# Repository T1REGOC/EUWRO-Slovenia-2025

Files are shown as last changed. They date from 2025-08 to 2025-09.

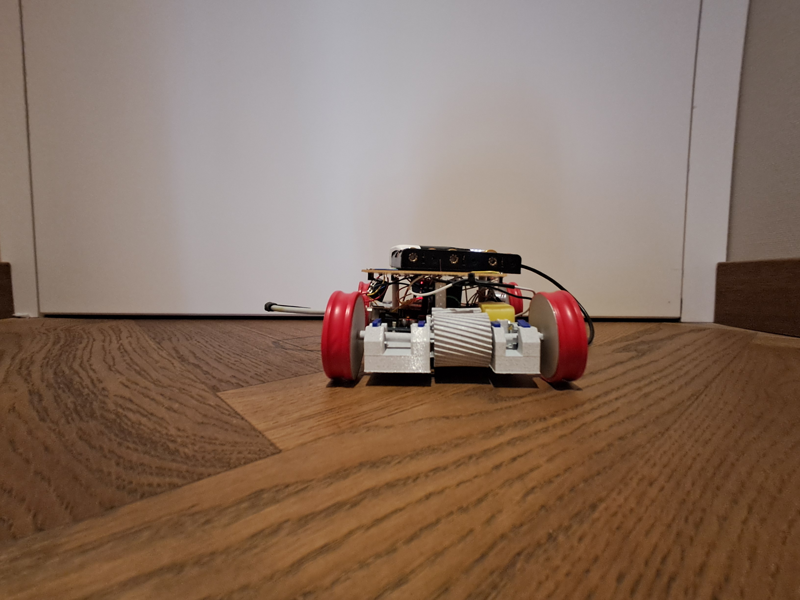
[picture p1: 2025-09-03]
Vehicle photos/Rear.jpg

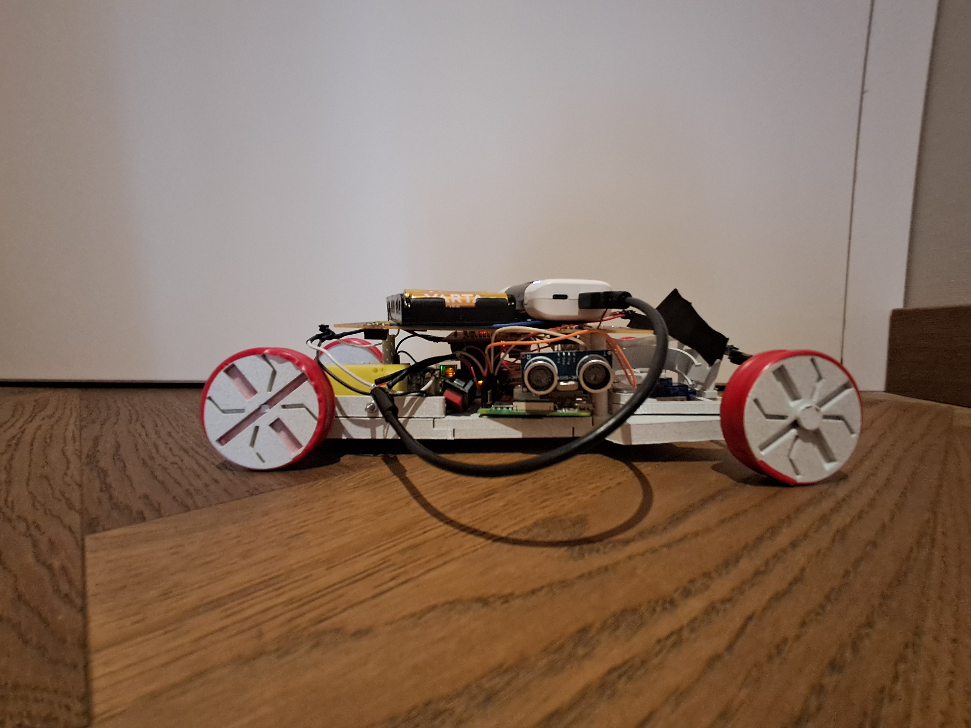
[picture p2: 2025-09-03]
Vehicle photos/Right.jpg

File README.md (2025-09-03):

This is a completely new, special repository made just for the competition in Slovenia, but here is an older version:

https://github.com/T1REGOC/WRO-2025-Season

# REGOČ | EUWRO-Slovenia

<center> <center>

## TABLE OF CONTENT

| Section  | Explanation |
| --  | -- |
| [PROBLEM](#problem)  | Adressing the task of the competition. |
| [ENGINEERING MATERIALS](#engineering-materials)  | The list of everything we used. |
| [MOBILITY MANAGMENT](#mobility-managment)  | [Driving](#driving),  [steering](#steering)| 
| [POWER AND SENSE MANAGMENT](#power-and-sense-managment)  |  [Power supply](#power-supply), [sensorics](#sensorics)  |
| [PICUTRES](#pictures)  |  [Team pictures](#team-pictures), [vehicle pictures](#vehicle-pictures)  |
| [ASSEMBLY INSTRUCIONS ](#assembly-instructions)  |  [Hardware](#hardware), [software](#software)  | 
| ---| --- |
| [3D FILES](https://github.com/T1REGOC/EUWRO-Slovenia-2025/tree/main/3d%20Models)| Files of our robot. |
| [SRC](https://github.com/T1REGOC/EUWRO-Slovenia-2025/tree/main/src) |Code. |
| [SCHEMES](https://github.com/T1REGOC/EUWRO-Slovenia-2025/tree/main/schemes)| Schemes of...  |
| [VIDEOS](https://github.com/T1REGOC/EUWRO-Slovenia-2025/tree/main/videos)| Videos of our robot. |

# PROBLEM
The goal of the Future Engineers WRO category is to design a fully autonomous vehicle that completes two different challenges in 3 minutes. The direction of the vehicles movement, position of the interior walls  and their size in both challenges is randomized before the start of the round, so the vehicle should recognize whether to turn left or right by itself. 
This is our playfield:
<br><br>
    


<br><br>
### OPEN CHALLENGE
In the open challenge, once the robot starts, its goal is to complete 3 laps around the map while avoiding the walls and finish in the same zone it started in.
For the Open Challenge we use ultrasonic sensors to make sure the vehicle is centered at all times, that is why we have ultrasonic sensors on both sides, and while the vehicle is centering it also looks for a pattern using the camera.
We needed to take a look at the map again:



By thinking a little bit you can see that if your direction is clockwise you will pass the lines always going orange first and then blue, but if you are going counter-clockwise you will always go blue first and then orange. We did not recognize this at first, but after a few months of working on the robot it was almost like a key, because our most unpredictable sensor from the last robot(the color sensor APDS-9960) did not give accurate results so we would want to remove it in this one. That is when we got the idea that the passing of the lines(orange-blue or blue-orange) is a pattern and we could use tensorflow for that because what is a machine learning model best at? You're right, looking for patterns. Using tensorflow we would make a model that had these possible outputs(orange-blue, blue-orange or none), it is pretty straight-forward to how we would adapt looking at the output, if the camera saw orange-blue it steers right, blue-orange it steers left, then we count the times that we passed the lines and when it hit 12(3 laps) we stop.

### OBSTACLE CHALLENGE 
In the obstacle challenge, once the robot starts, its goal is again to complete 3 laps but now other than avoiding walls it has to avoid red and green pillars which are in the way. Depending on the color 
it passes the pillars either from the left or the right (robot passes pillar on the right if he sees red, and on the left if he sees green). Once the 3 laps are complete and robot is back in its starting area it should parallely park in the previously set
parking spot. The parking spot is 1.5x the lenght of the vehicle. The vehicle may also start from the parking spot. 
So how did we do it? We first thought about using just RGB and opencv, but we researched about the color formats and we did not want to use RGB after that because we found the superior one: HSV(Hue, Saturation, Value). So you might ask why we use this instead of RGB, its simple:
1. It seperates color(hue) from brightness(value) and saturation colour intensity.
2. It is more robust to lighting changes than RGB.
3. It makes it easier to define color ranges for masking
4. RGB mixes color and brightness, so the same color can look very different under different lighting.
HSV allowed us to filter by hue, making color detection more reliable. But we dont want to solely depend on just opencv, we want to make it both more reliable and more educational therefore we added tensorflow. This time we made a model with tensorflow that looked for green or red pillars, so then in the code we made it so even though opencv saw the pillar it has no power because tensorflow was our priority. So the only way that a pillar would be detected and accepted is for our tensorflow model to find it.
Now we fixed the problem with the pillars, we gotta get the parking right, for parking we use ultrasonic sensors and also decided to use 2 instead of 1 ultrasonic sensors on the sides(you will see why in a bit), so depending on what is our steering side the parking will always be opposite(if you steer right the parking is on the left) and we would use that to our advantage, so for the parking after the last steering we would "line up" the vehicle for parking by looking at the differences of distance that the ultrasonic sensors give on the same side, so for example if the vehicle is at a 30 degree angle from the wall back sensor would give 3cm and the front one would be 8cm, what we would do in this scenario is steer the vehicle depending on which number is bigger and which side it was, and we would do this until the difference would be under 2cm.
#### PARKING
Now that we are lined up to the wall we dont want to steer until we actually need to park in, so now we look for the parking also using ultrasonic sensors but now looking solely on the back side sensor, why? Because the parking walls are 20cm wide and passing by our sensor would see this(25,25,27,28,28,2,2,28) so if you dont understand those would be the example readings from the sensor and we knew when we hit the parking spot when we would hit a "drastic change" often going in a number that is under 10cm, but we cant steer yet because we hit the first part of the parking and we want to parralel park so we need to hit the second part of the parking, we just go straight and look for another drastic change again, when we see it that means that the back side sensor(almost where the back wheels are) is at the second part of the parking, so now we reverse and steer until our back sensor hits under 5cm and then go forward and steer to line up.
   
# ENGINEERING MATERIALS
- Servo SG90 (23 x 12 x 29 mm) ( Why we chose it: reliable, small, previusly available to us )
  datasheet: http://www.ee.ic.ac.uk/pcheung/teaching/DE1_EE/stores/sg90_datasheet.pdf


- Yellow TT Gear Motor (71 × 22 × 37 mm) ( Why we chose it: enough torque (further explained later on) , previously available to us, reliable )
  datasheet: https://media.digikey.com/pdf/Data%20Sheets/Adafruit%20PDFs/3777_Web.pdf 


- HC - SRO4 Ultrasonic sensor (x6) (43 x 20 x 15 mm)
  datasheet: https://cdn.sparkfun.com/datasheets/Sensors/Proximity/HCSR04.pdf


- Raspberry Pi Camera v2 (25mm x 23mm x 9mm)
  datasheet: https://www.farnell.com/datasheets/2056179.pdf?_ga=1.152577328.880870297.1479740269


- DHT11 (15.5 x 12 x 5.5 mm)
  datasheet: https://www.mouser.com/datasheet/2/758/DHT11-Technical-Data-Sheet-Translated-Version-1143054.pdf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


- Arduino Uno (69 x 54 mm)
  datasheet: https://docs.arduino.cc/resources/datasheets/A000066-datasheet.pdf


- Raspbbery Pi 4 (86 x 57 mm)
  datasheet: https://datasheets.raspberrypi.com/rpi4/raspberry-pi-4-datasheet.pdf


-PLA (3D printing materials)

# MOBILITY MANAGMENT
Considering we 3D designed everything ourselves, we decided to split the vehicle in three parts: the front ( steering ), the rear  ( drive ) and the middle ( connection beetween two ).They are connected so that the top part of the drive and the bottom part of the middle part allign and then we screw through both of them.  We did that so that if there is failure for example the steering, we do not have to print it all again, but just the steering part. That is also why we tried to design everything so that we can tighten it by screws. 

The round pillars that rise from the pplatforms are holders for the protoboard. 

Because of our modularity, considering the robot isn't printed as whole it bends more, so we decided to print little bend preventers. They are designed so that thay fight very tightly over the connction of the segments. They are U shaped, 20 mm wide. 

## DRIVING
For the driving power, the motor, we decided to go with TT Yellow Gear Motor because it was strong enough, reliable, affordabble and available to us. 

Motor torgue – 0,8kg / cm 
Gear output torque – 1.6kg/cm  ( gear ratio == 1:2 ) 
Torque on wheels – 1.4 kg/cm ( gear output torque  - min. 10%)

Formula for torque when the gear ratio is 1:2

T = (Mt * 2) – (Mt*2 *10%)

T = Final torque on wheels
Mt – Motor torque

We stabillised it to the platform by designing a holder for it. It is placed longitunally. 
With two helix gears, whose ratio is 1:2 (so that we gain torque since the speed is not as necessary), we created a transmission.
Why helix gears?
We thought about using double helix gears because they have a great grip, but considering that we wanted most of the parts to be modular, the double helix gears would be harder to dismantle and mantle each time. 
The first, main gear has 16 teeth and is 15.6mm in diameter, 32.5mm in lenght. From one side it is span by the motor, and from the other, just to stop its lean it is supported by a little holder. 
To the second, drive gear (30mm diameter, 32.5mm, 32 teeth ), we created a plus shaped hole since we needed the shaft to rotate with the gear. The two shafts are also plus shaped and connected by a plus shaped connector. They have plates so that they don't move left / right thorugh the gear. At the end there is a rectangular hold for the wheels. 

Here it is all together:

 

## STEERING
For the steering, we went with a always reliable, stable, small, affordable and available SG90 servo motor. We decided on the Ackermann's steering system since it
seemed more stable than pivot point turning or others. 
This is an example of the Ackermann's steering system.



You design a servo addon that rotates the middle connector. The two side motor hubs are pivotted at one point and on the other connected to the middle shaft. On the hubs go wheels. When the servo rotates, the addon rotates with it and moves the connector left aand right. Then the motor hubs rotate because of the pivot on the other side.  

Considering that upfront we don't have driving power, the wheels must be able to rotate freely. So the shaft that they go on is a bit lose, so the wheels have the abilty to rotate and then just tighten it up with a designed screw. The wheels will spin when the 
drive wheels start to spin.

Because thec camera is infront of the steering, but has to cross over the steering to get to the raspberry, we designed a little bridge so that the camera cable doesn't block our steering. 

Max. Steering angle == 30°



<br><br><br>
Here it is all together:



# POWER AND SENSE MANAGMENT

Electrical scheme



## POWER SUPPLY
As for the competition at the national championship in Samobor, we will use a portable charger to power our autonomous robot. The charger we use is small so it will not take up too much space on the robot. This charger also has an on/off button, which can be used to turn the robot on and off. This charger outputs 5V and 3A, which is ideal for powering our autonomous robot. Portable chargers also use a BMS (battery management system) which ensures that the battery is safe and reliable. With the BMS, we can see things like battery charge, battery capacity, and we can get feedback about any problems with the battery. Our charger has a light indicator for battery charge. BMS is also used to balance cells (if some are discharged or overcharged), prevents overvoltage, underdischarge, overcurrent, and overheating.

---
## SENSORICS

- Selection


The selection of sensors for our project was carried out systematically. For each potential component, we carefully considered not only its advantages but also every possible limitation or drawback it could introduce. This iterative process—selecting, evaluating, and refining—ensured that the final sensor set was both practical and effective for our goals.

- Ultrasonic sensors
  
One of the key design decisions was to integrate two ultrasonic sensors, positioned on both sides of the robot instead of relying on a single unit. This configuration allows the robot to align itself precisely with walls, which can then be leveraged for autonomous steering without depending solely on the camera system. By doing so, we enhanced both the reliability and independence of the navigation process.

- Digital Temperature and Humidity sensor
  
Additionally, we incorporated a DHT11 sensor to measure ambient temperature and humidity. These values directly influence the speed of sound in air, and by accounting for them, we can improve the accuracy of distance measurements from the ultrasonic sensors. This consideration highlights the importance we placed on precision and robustness in the sensor design. Therefore instead of the fixed speed of sound at 343m/s we made it a variable, and this is the formula we used:

`Speed_of_sound(m/s) = 331.4 + 0.6 * temperature(°C) + 0.0124 * Humidity(%)`

---
# PICTURES
## TEAM PICTURES
teamofficial

Left: Gabriel , Middle: David, Right: Vedran

funnypic

Funny picture

## VEHICLE PICTURES
Rear



Left



Right



Top


Front


<br><br><br>
# ASSEMBLY INSTRUCTIONS
## HARDWARE

List of materials:
All of the 3d prints, and engineering materials + M2 & M3 set of bolts amd nuts

### 1. PLATFORM
Place the front / rear platform next to the middle one so that the holes for the screwes corespond and then screw it. 
<br>

### 2. DRIVE
1. Install the motor inside his holder.
    - Put the motor in the holder and screw it.
    - Don't screw the holder to the platform!
2. Insert the small gear in the holder and the motor shaft on the other end.
3. Install the motor to the platform.
4. Big gear preparation
    - Take the two shafts and insert them in the gear until they are connected.
    - Put the cards on the shaft ( 2 on each side) corespondingly to the card holder holders.
5. Lower the big gear with card holders in their place.
6. Screw the cards to their holders.
7. Place the wheels at the end of the shaft.
<br><br>

### 3. STEERING
1. Place the servo in its place and screw it.
2. Place the left and the right arms in their position
3. Place the connector so that it captures both the left and the right arm.
4. Cover them up with coresponding covers.
5. Place the servo addon so that it connects from the middle of the connector to the servo.

## SOFTWARE
#### 1. Arduino Uno
1. Arduino IDE
    - Download and install the official Arduino IDE from [https://www.arduino.cc/en/software]
    - This software allows you to write code(called sketches), compile them, and upload them to your Arduino board

    **Setup**
    - Connect the Arduino Uno to your computer using a USB cable
    - Open the Arduino IDE and select your board:
        - Go to Tools - Board - Arduino AVR Boards - Arduino Uno

    **Uploading the program**
    - Open the sketch you want to run, for this robot specifically you want the one that says "THIS RUNS ON THE ARDUINO UNO"
    - Click the Upload button and the IDE will compile the code and upload it to the Arduino
    
    **Auto-running the program**
    - Once the code is uploaded the sketch is stored in the Arduino memory
    - Whenever the board is powered, the program will automatically start running, therefore you dont need any additional setup
    The Arduino Uno is successfully setup!

#### 2. Raspberry Pi 4
1. Raspberry Pi OS
    - Download and install the official Raspberry Pi Imager from[https://www.raspberrypi.com/software/]
    - This software will allow you to download and write various operating systems to a microSD card
    - In this case you want to choose Raspbian on the Operating System tab, and then choose your desired SD Card. When the OS is written on the SD Card you will want to insert it into the SD Card compartment on the Raspberry Pi 4

    **Setup**
    - You can either connect the Raspberry Pi to a monitor using its micro HDMI output or do everything with VNC(without contact). Since using a monitor and a micro HDMI cable is more intuitive you can use that option.
    - Now you will want to transfer the codes that say "THIS RUNS ON THE RASPBERRY PI" onto the Raspberry Pi 4.

    **Auto-running the program on start**
    - Open command prompt and run `sudo nano /etc/rc.local`
    
    Explanation:
    - sudo - run with administrator rights(needed because /etc/rc.local is a system file)
    - nano - text editor used to open the file
    - /etc/rc.local - a script that runs automatically at the end of every boot process on Linux

    - Now you will want to add the line
     `sudo bash -c 'sudo python3 /home/pi/<<directory>>/<<filename.py>>' &` before the line `exit 0` and save and close

    Explanation:
    - sudo - run as root(administrator)
    - bash -c ' ... ' - tells bash to run the command inside the quotes
    sudo python3 /home/pi/.../filename.py - runs the Python program as root using python3
    - & - runs the command in the background, so the system can continue booting without waiting for Python script to finish

    Reboot the Raspberry Pi and it will be ready to use!

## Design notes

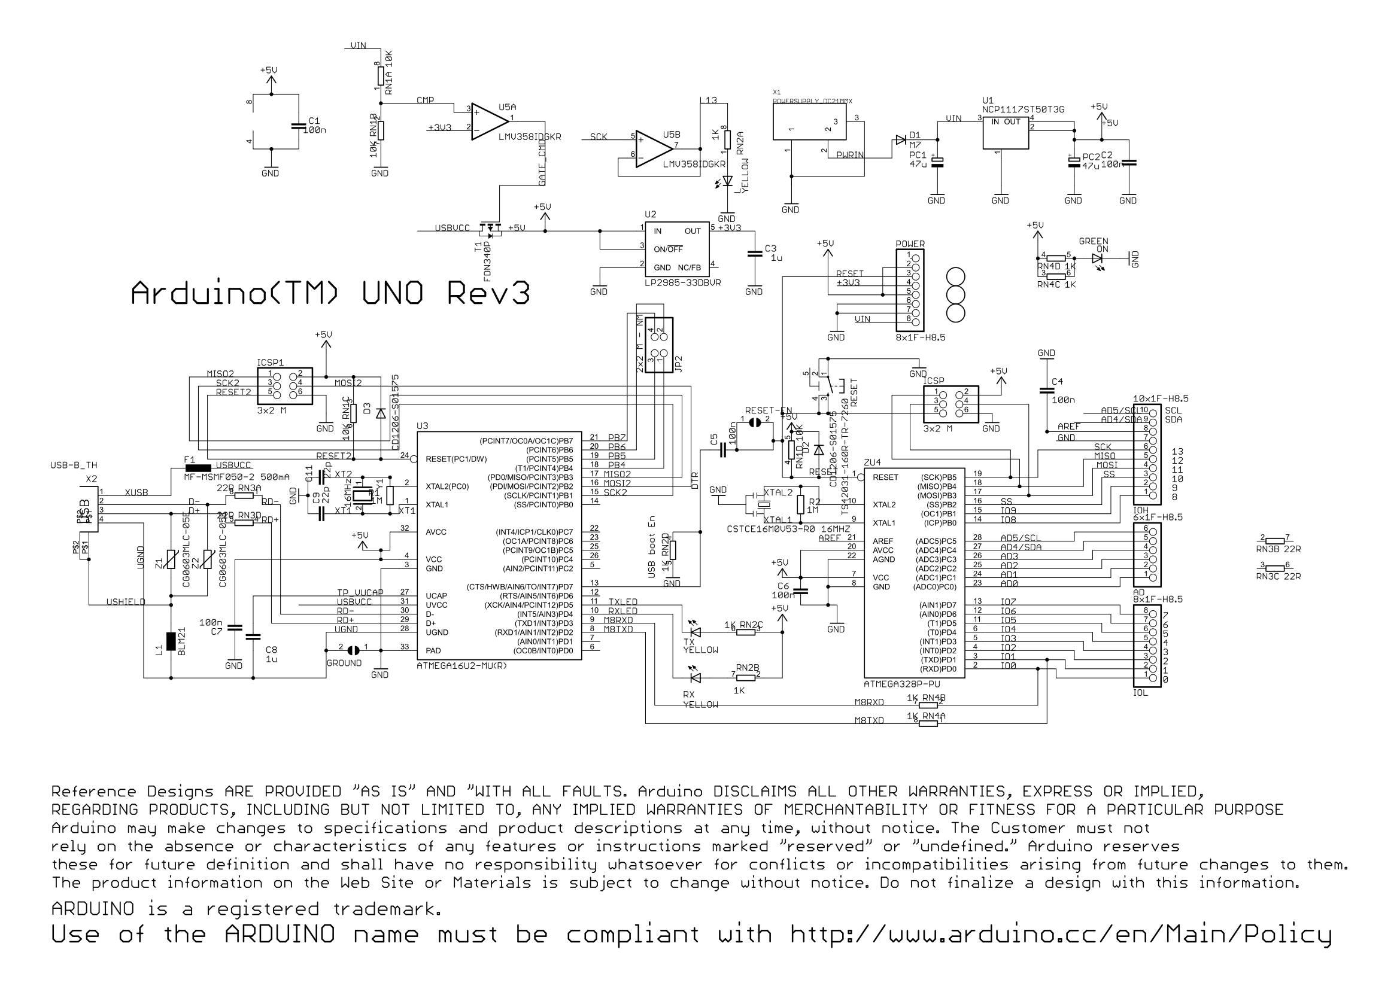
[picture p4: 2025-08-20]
schemes/Arduino_Uno_Rev3-schematic-1.png

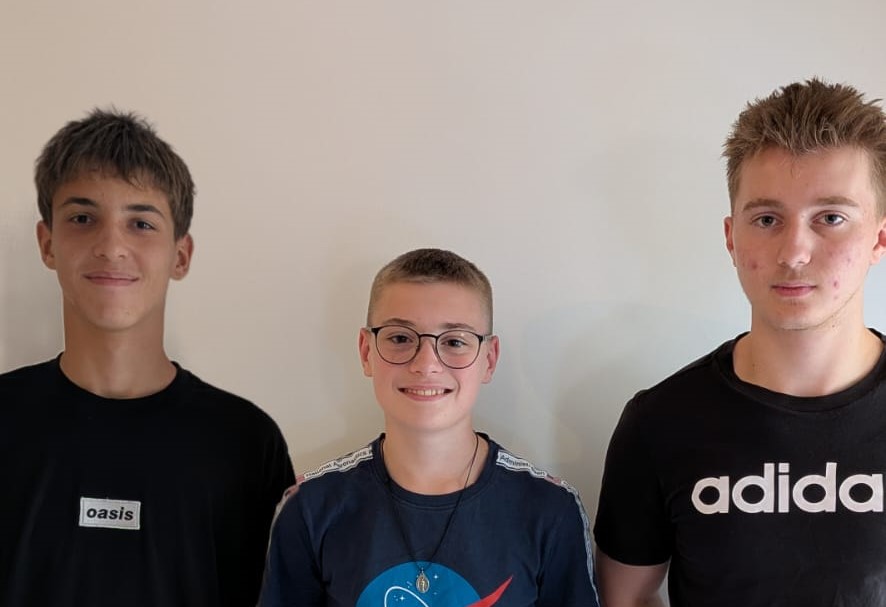
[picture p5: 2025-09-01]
Team photos/teamofficial.jpeg

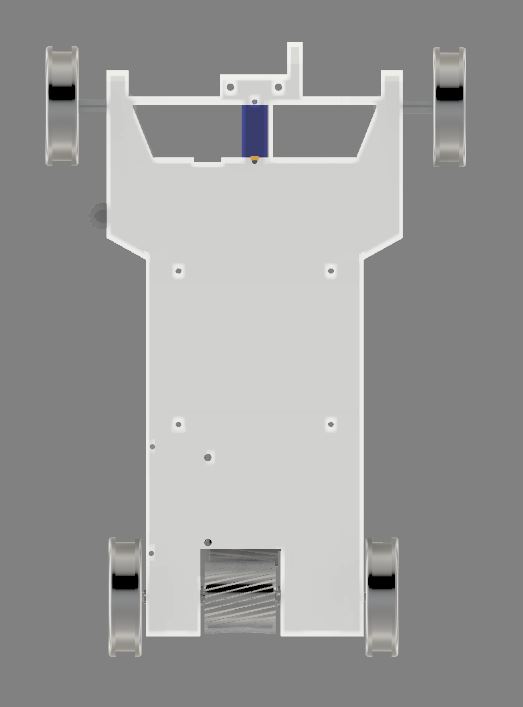
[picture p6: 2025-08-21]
Vehicle photos/bottom.JPG

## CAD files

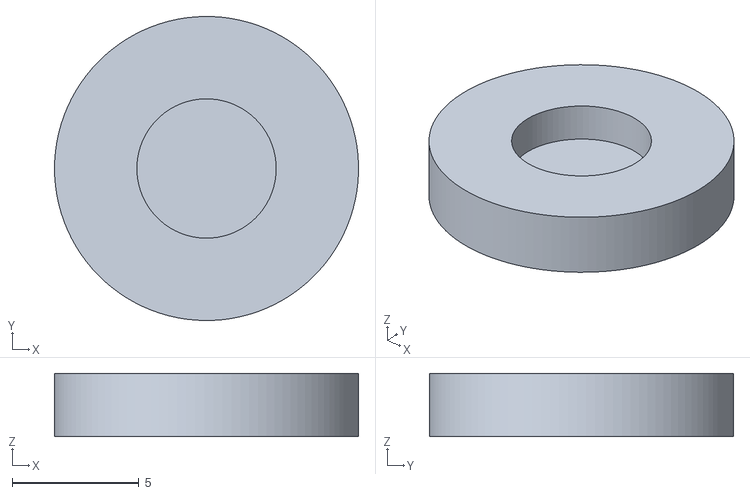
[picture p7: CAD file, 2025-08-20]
3d Models/poklopacox2.stl
12.0 x 12.0 x 2.50

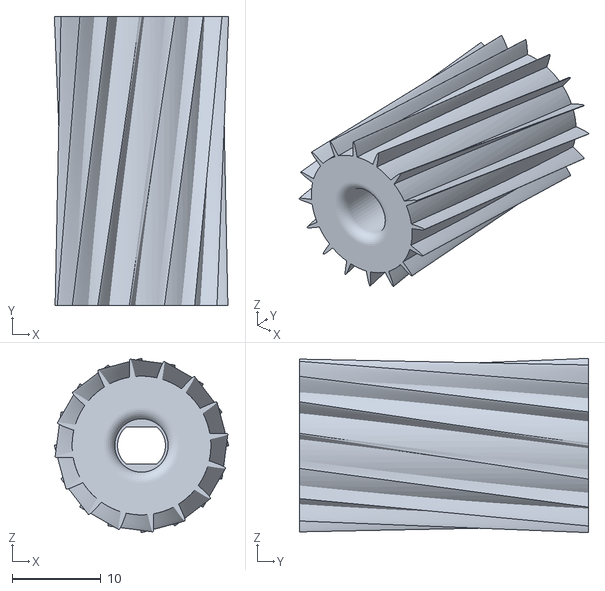
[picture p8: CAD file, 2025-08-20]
3d Models/maligear.stl
19.6 x 32.5 x 19.6

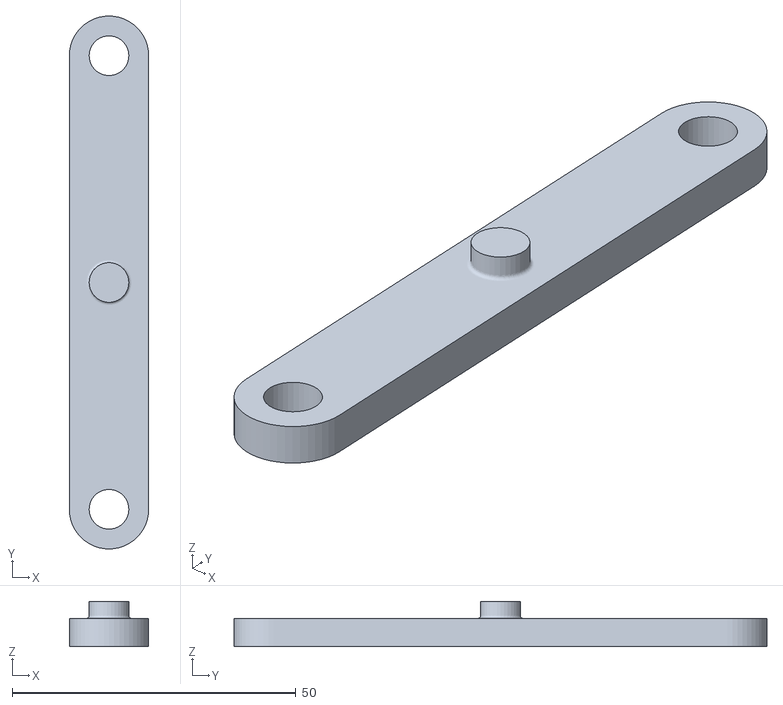
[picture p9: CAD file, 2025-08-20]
3d Models/connector.stl
14.0 x 94.0 x 8.00

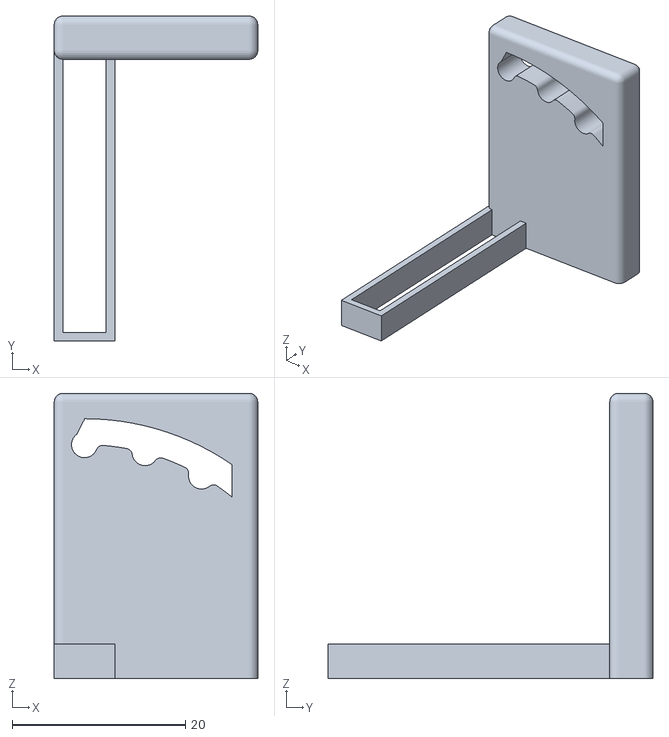
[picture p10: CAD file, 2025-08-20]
3d Models/kamerapoomično.stl
23.5 x 37.5 x 32.9

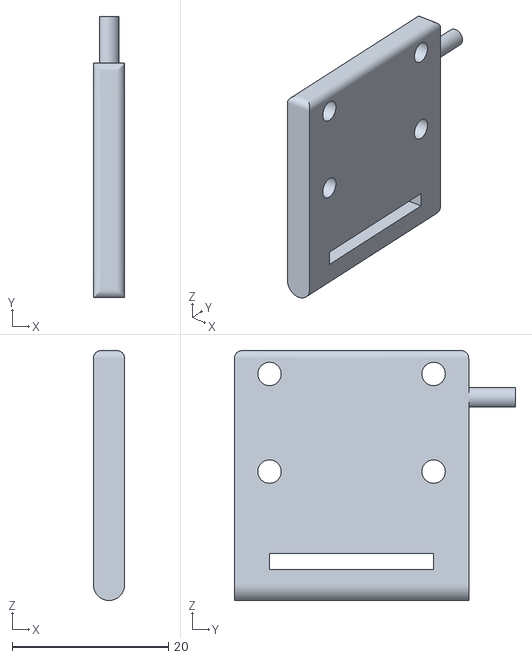
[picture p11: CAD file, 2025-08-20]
3d Models/kameraholder.stl
4.00 x 36.0 x 32.0

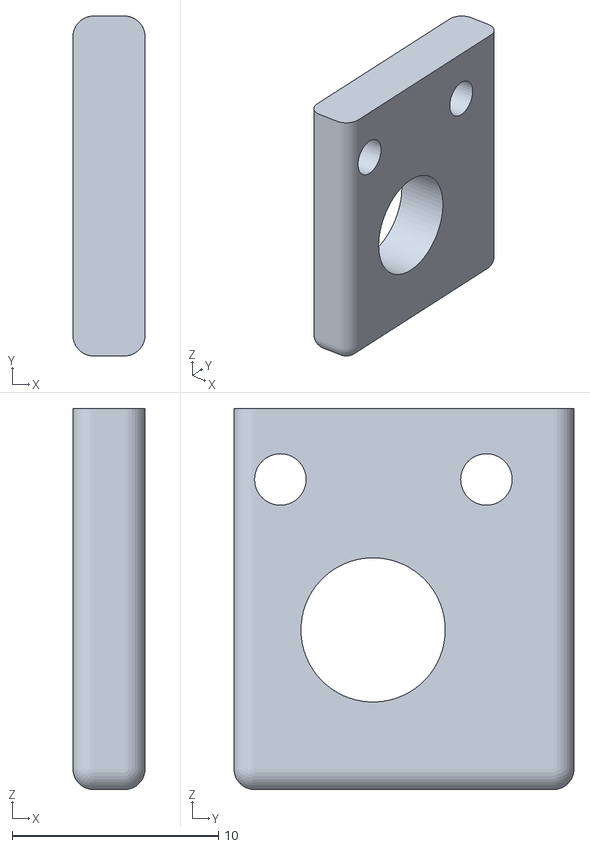
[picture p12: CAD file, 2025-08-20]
3d Models/kartica.stl
3.50 x 16.5 x 18.5

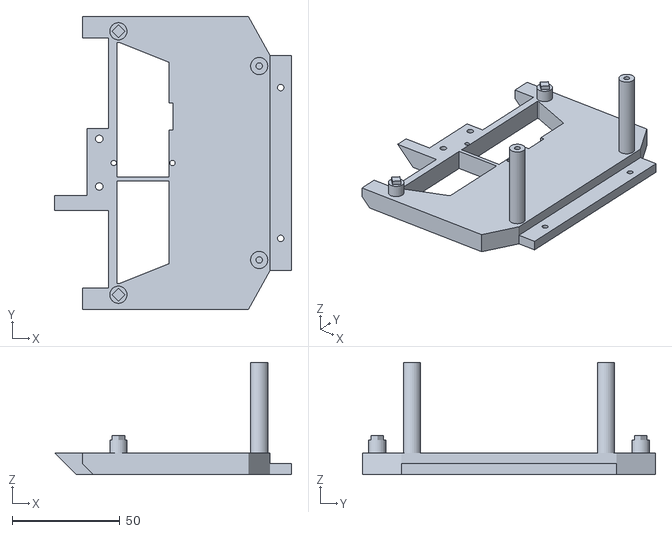
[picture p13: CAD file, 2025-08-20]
3d Models/tijeloskretanje.stl
110.0 x 136.0 x 52.0

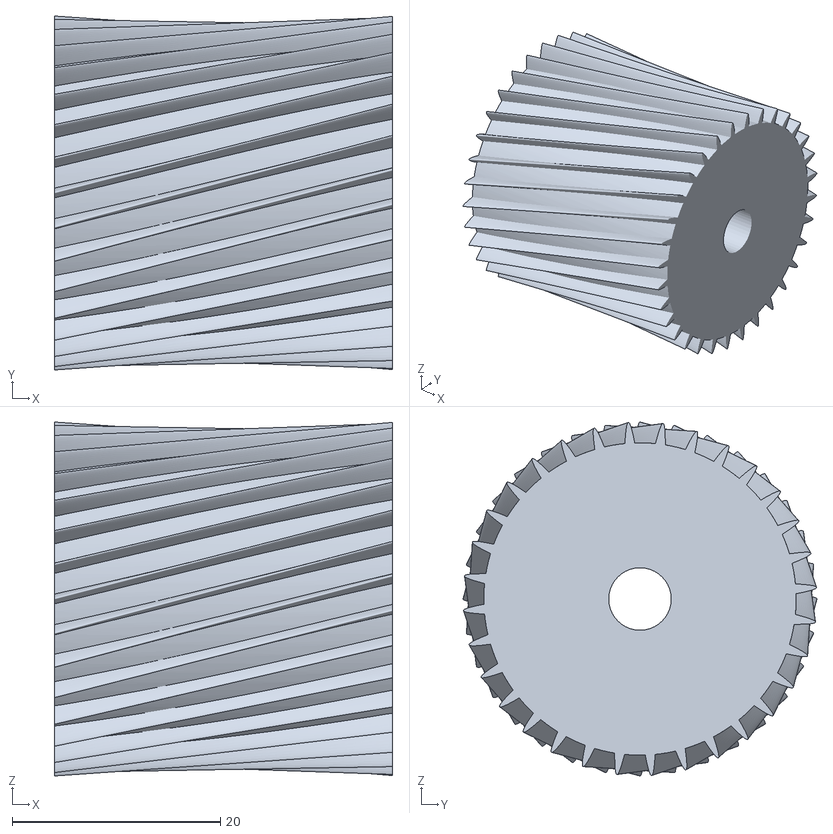
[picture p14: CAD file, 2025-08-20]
3d Models/velikigear.stl
32.5 x 34.0 x 34.0

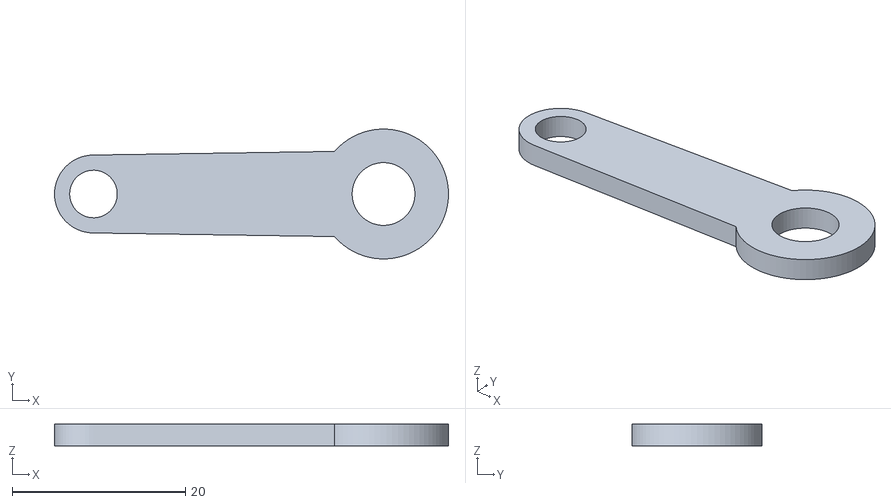
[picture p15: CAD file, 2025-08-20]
3d Models/servoaddon.stl
45.5 x 15.0 x 2.50

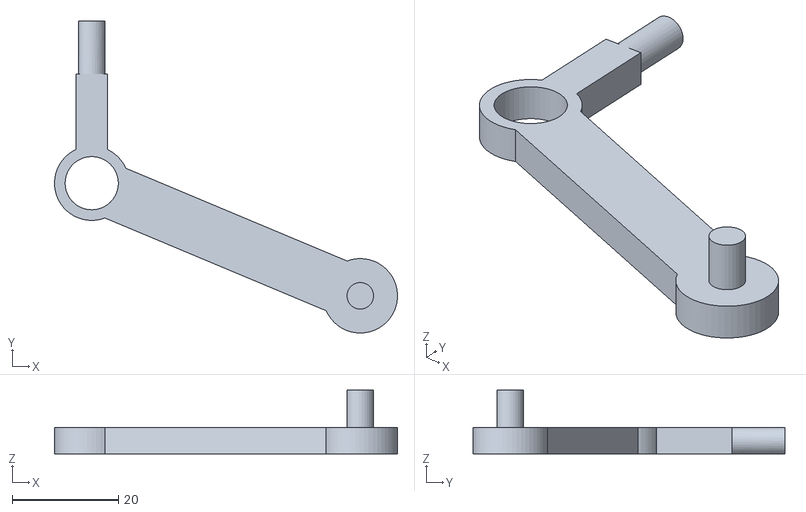
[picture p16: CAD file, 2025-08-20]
3d Models/desninosač.stl
64.5 x 58.7 x 12.0

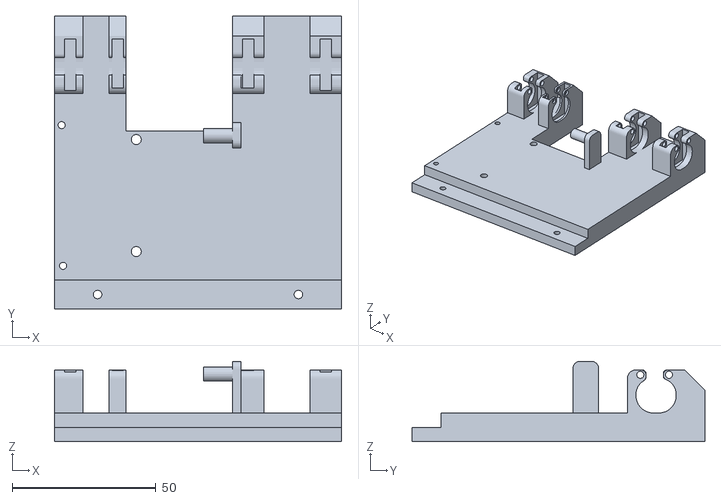
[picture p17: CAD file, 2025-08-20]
3d Models/tijelopogon.stl
100.0 x 102.0 x 28.0

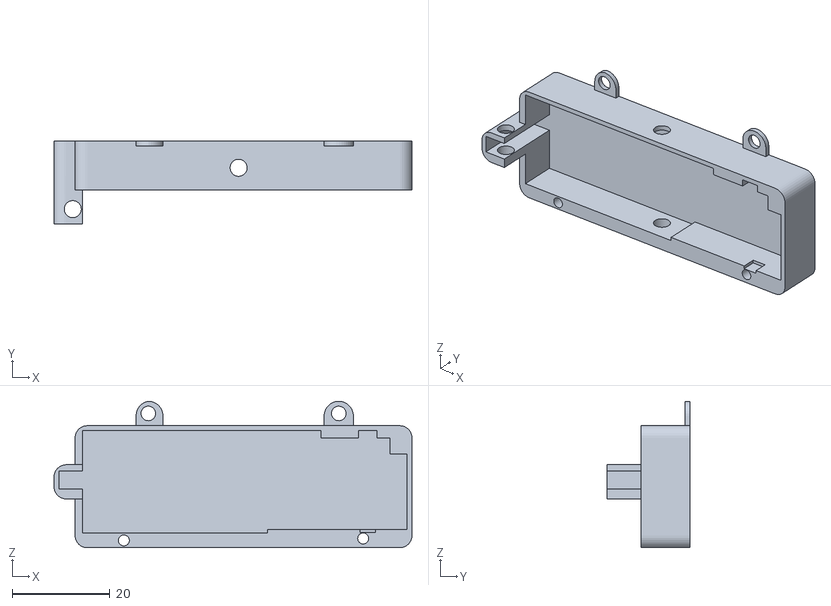
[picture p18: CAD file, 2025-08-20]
3d Models/motorholder.stl
73.3 x 17.0 x 30.0

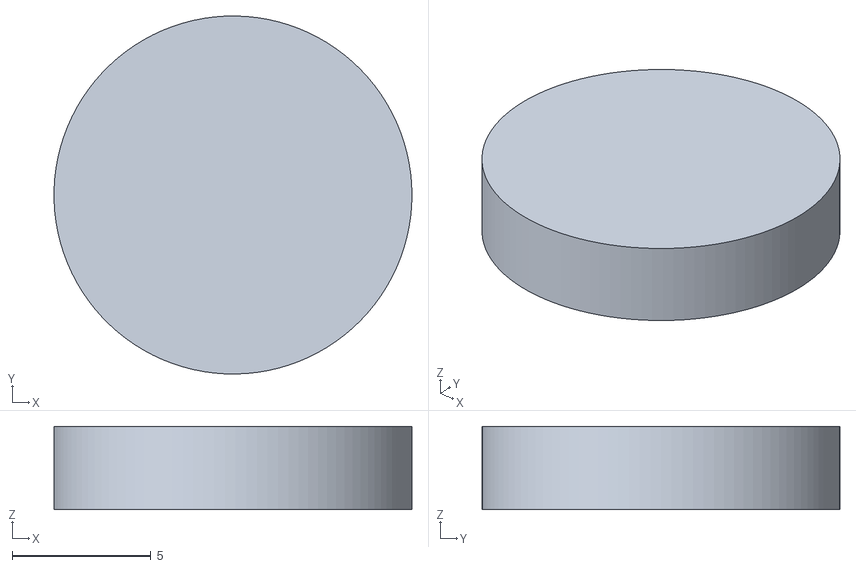
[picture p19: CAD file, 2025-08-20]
3d Models/poklopackx2.stl
12.9 x 12.9 x 3.00

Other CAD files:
3d Models/lijevinosač.stl

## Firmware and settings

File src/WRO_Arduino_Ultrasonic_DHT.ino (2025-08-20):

// THIS CODE IS FOR THE ARDUINO UNO //
//            TEAM REGOC            //
#include <DHT11.h>  // Include the DHT sensor library to read temperature and humidity data.
#include <NewPing.h>  // Include the NewPing library to control ultrasonic sensors.
#include <Wire.h>
#include <Servo.h>

#define APDS9960_ADDR 0x39 // I2C address for the APDS9960 sensor.
#define ENABLE_REG 0x80 // Register address for enabling the APDS9960 sensor.
#define ATIME_REG 0x81 // Register address for the APDS9960 sensor's integration time.
#define CONTROL_REG 0x8F // Register address for controlling the APDS9960 sensors gain and other settings.
#define CDATAL_REG 0x94 // Register address for reading color data from the APDS9960 sensor.
#define trigPin 2  // The trigger pin for all the ultrasonic sensors (sending the pulse).
#define echoPin1 3  // The echo pin for the first ultrasonic sensor.
#define echoPin2 5  // The echo pin for the second ultrasonic sensor.
#define echoPin3 6  // The echo pin for the third ultrasonic sensor.
#define echoPin4 7  // The echo pin for the fourth ultrasonic sensor.
#define echoPin5 8  // The echo pin for the fifth ultrasonic sensor.
#define echoPin6 9  // The echo pin for the sixth ultrasonic sensor.
#define dhtPin 4  // The data pin for the DHT22 sensor.
#define maximum 400  // Maximum range of the ultrasonic sensors in cm.

DHT11 dht11(4); // Initialize the DHT11 sensor object on pin 4.

Servo stmotor;
//steering motors for detection
#define m1 12
#define m2 A0
#define m3 A1
#define m4 A2

//speed motors
#define s1 10
#define s2 11

// power pins for speed
#define p A3

NewPing sonar1(trigPin, echoPin1, maximum);  // Initialize the first ultrasonic sensor.
NewPing sonar2(trigPin, echoPin2, maximum);  // Initialize the second ultrasonic sensor.
NewPing sonar3(trigPin, echoPin3, maximum);  // Initialize the third ultrasonic sensor.
NewPing sonar4(trigPin, echoPin4, maximum);  // Initialize the fourth ultrasonic sensor.
NewPing sonar5(trigPin, echoPin5, maximum);  // Initialize the fifth ultrasonic sensor.
NewPing sonar6(trigPin, echoPin6, maximum);  // Initialize the sixth ultrasonic sensor.

int readDHT, temp, hum, SoS;  // Variables for reading temperature and humidity, and calculating speed of sound.
float duration1, duration2, duration3, duration4, duration5, duration6;  // Variables to store the pulse duration from each ultrasonic sensor.
float distance1, distance2, distance3, distance4, distance5, distance6;  // Variables to store the calculated distance from each sensor.
int prev_r = 0, prev_g = 0, prev_b = 0; // Previous detected colors

void setup() {
  Serial.begin(9600);  // Start serial communication for debugging and output.

  Wire.begin(); // Initialize I2C communication.

  apds_write(ENABLE_REG, 0b00000011); // Enable the APDS9960 sensor.
  apds_write(ATIME_REG, 0xDB); // Set the integration time for the APDS9960 sensor.
  apds_write(CONTROL_REG, 0x01); // Set the gain for the APDS9960 sensor.
  // Read data from the DHT22 sensor.
  readDHT = dht11.readTemperatureAndHumidity(temp, hum);  
  
  // Calculate the speed of sound based on temperature and humidity using the formula.
  SoS = 331.4 + (0.6 * temp) + (0.0124 * hum);

}

void loop() {
  delay(120);

  uint16_t c = read16(CDATAL_REG); // Read the color data from the APDS9960 sensor.
  uint16_t r= read16(CDATAL_REG + 2); // Read the red color data.
  uint16_t g= read16(CDATAL_REG + 4); // Read the green color data.
  uint16_t b= read16(CDATAL_REG + 6); // Read the blue color data.

  int r255 = (c > 0) ? constrain((float)r / c * 255, 0, 255) : 0; // Convert the red color data to a value between 0 and 255.
  int g255 = (c > 0) ? constrain((float)g / c * 255, 0, 255) : 0; // Convert the green color data to a value between 0 and 255.
  int b255 = (c > 0) ? constrain((float)b / c * 255, 0, 255) : 0; // Convert the blue color data to a value between 0 and 255.

  int diff = abs(r255 - prev_r) + abs(g255 - prev_g) + abs(b255 - prev_b); // Calculate the difference in color values to detect significant changes.
  
  // Get the pulse duration from the first ultrasonic sensor and convert it to seconds.
  duration1 = sonar1.ping_median(2);  // Use median of 2 pings to avoid .
  duration1 = duration1 / 1000000;  // Convert microseconds to seconds.
  
  // Calculate the distance using the formula: distance = (speed of sound * duration) / 2.
  distance1 = (SoS * duration1) / 2;

  // Repeat the process for the other five ultrasonic sensors.
  duration2 = sonar2.ping_median(2);
  duration2 = duration2 / 1000000;
  distance2 = (SoS * duration2) / 2;
  
  duration3 = sonar3.ping_median(2);
  duration3 = duration3 / 1000000;
  distance3 = (SoS * duration3) / 2;
  
  duration4 = sonar4.ping_median(2);
  duration4 = duration4 / 1000000;
  distance4 = (SoS * duration4) / 2;
  
  duration5 = sonar5.ping_median(2);
  duration5 = duration5 / 1000000;
  distance5 = (SoS * duration5) / 2;
  
  duration6 = sonar6.ping_median(2);
  duration6 = duration6 / 1000000;
  distance6 = (SoS * duration6) / 2;

  speed();
  if (speed != prev_speed){ // Check if speed has changed
    switch(speed){
      case "01":
        analogWrite(p, 64); // Set speed to 25%
        break;
      
      case "10":
        analogWrite(p, 128); // Set speed to 50%
        break;
      
      case "11":
        analogWrite(p, 255); // Set speed to 100%
        break;
    }
  }

  steering();
  if (steering != prev_steering){ // Check if steering has changed
    switch(steering){
      case "0000":
        //off
        break;

      case "0001":
        //l(low)
        stmotor(75); // Set steering motor to low left
        break;

      case "0010":
        //l(mid)
        stmotor(60); // Set steering motor to mid left
        break;

      case "0011":
        //l(full)
        stmotor(45); // Set steering motor to full left
        break;

      case "0100":
        //s(straight)
        stmotor(90); // Set steering motor to straight
        break;

      case "0101":
        //r(low)
        stmotor(105); // Set steering motor to low right
        break;

      case "0110":
        //r(mid)
        stmotor(120); // Set steering motor to mid right
        break;

      case "0111":
        //r(full)
        stmotor(135); // Set steering motor to full right
        break;
    }

  }
  prev_speed = speed; 
  prev_steering = steering;
}


void speed(){
  if (analogRead(s1) > 40){
    s1 = 1; // If the analog reading from s1 is greater than 40, set s1 to 1.
  }
  if (analogRead(s2) > 40){
    s2 = 1; // If the analog reading from s2 is greater than 40, set s2 to 1.
  }
  speed = String(String(m1) + String(m2)); // Combine the values of s1 and s2 to form the speed string.
  return speed
}

void steering(){
  if(analogRead(m1) > 40){
    m1 = 1; // If the analog reading from m1 is greater than 40, set m1 to 1.
  }
  if(analogRead(m2) > 40){
    m2 = 1; // If the analog reading from m2 is greater than 40, set m2 to 1.
  }
  if(analogRead(m3) > 40){
    m3 = 1; // If the analog reading from m3 is greater than 40, set m3 to 1.
  }
  if(analogRead(m4) > 40){
    m4 = 1; // If the analog reading from m4 is greater than 40, set m4 to 1.
  }
  steering = String(String(m1)+String(m2)+String(m3)+String(m4)); // Combine the values of m1, m2, m3, and m4 to form the steering string.
  return steering
}

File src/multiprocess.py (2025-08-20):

## THIS CODE IS FOR THE RASPBERRY PI ##
            ## TEAM REGOC ##

import multiprocessing # Importing the multiprocessing module
import WRO_logic # Importing the WRO_logic module for the main logic of the program
import SerialWRO # Importing the SerialWRO module for serial communication

if __name__ == "__main__": 
    manager = multiprocessing.Manager() # Creating a manager to handle shared data between processes
    values = manager.list([0, 0, 0, 0, 0, 0, '', 0, 0])  # Shared list for sensor values
                # sensor1, sensor2, sensor3, sensor4, sensor5, sensor6, way, blue(count), orange(count)
    p1 = multiprocessing.Process(target=WRO_logic.main, args=(values,)) # Main logic process
    p2 = multiprocessing.Process(target=SerialWRO.serial_reader, args=(values,)) # Serial reader process

    p1.start() # Starting the main logic process
    p2.start() # Starting the serial reader process

    p1.join() # Waiting for the main logic process to finish
    p2.join() # Waiting for the serial reader process to finish

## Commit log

2025-08-20 Assembly Instructions SW #1
2025-08-21 Sensorics and power management fixed
